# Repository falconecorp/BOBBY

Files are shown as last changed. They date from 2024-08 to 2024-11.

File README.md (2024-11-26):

# BOBBY
Bobby es un robot construido para competir en los juegos bonaerenses, en la categoría de Triatlón( Quita obstaculos - Sumo - Seguidor de linea ), por los estudiantes, Iago Botto, Dante Abel Canale, Lautaro Lammers y Lucas Chavez

[img_20240703_164955.md](https://github.com/user-attachments/files/17923314/img_20240703_164955.md)

## FUNCIONAMIENTO

### Seguidor de linea:
  Tenemos un sistema de sensores reflectivos QRE1113GR, en configuracion de array, que permite detectar con precisión, una linea blanca que representa el camino, y debemos recorrerlo en el menor tiempo posible
Utilizamos un algorimo de PD
~~~
  uint8_t PID(){
    int error = setpoint - lecturaQRE();
    int P = error * Kp;
    int D = (error - ultimo_error) * Kd;
    ultimo_error = error;
    float output = P + D;
    output = abs(output);
    output = map(output, 0, 25000, 0, limite_output);
    output = constrain(output, 0, limite_output);
    return (output);
  }
~~~
que nos permite poder variar los valores PWM enviados al motor, para seguir la linea correctamente

### Quita Obstáculos
  Nos encontramos con 5 sensores GP2Y0A02YK0F de distancia, que con un algoritmo y filtro digital, verificamos si hay un objeto o no. Agregado a esto, se utilizan 3 sensores de piso QRE1113GR, para evitar caernos de la pista
cuando atacamos a cada obstáculo.

### Sumo
  Aqui tenemos a nuestra categoría estrella, en esta disciplina, el robot es controlado por el usuario a través de una conexión Bluetooth entre un joystick de Ps3, y un modulo ESP32. Se compite contra otro robot en las mismas condiciones en un tatami.

## INFORME DE COSTES
#### Sensores
  -Sharp GP2Y0A02YK0F: 10.509$ c/u (starware)  (x5)    
  -Sensores de piso QRE1113GR: 969.37$ c/u (mouser)  (x8)    
  -impresion 3D: 8.000$ (300 gr)    
  -Motores AP&S SP6-260: 26.000$ c/u (AP&S)  (x2)    
  -Controladores BTS7960: 20.0000$ c/u (MercadoLibre)  (x2)    
  -ESP32: 7.329$ c/u (Starware)   (x1)    
  -Conexionado y cables: 20.000$ (it&t)    
#### Costo total: 187.626$
## FALLAS Y COSAS A MEJORAR
### organización
  -Problemas en el cálculo de tiempos.    
  -incumplimientos de los plazos acordados.    
  -falta de compromiso con el proyecto.    
  -falta de conocimientos previos para un proyecto de este calibre.    
  -subestimacion de los demas competidores.    

### programación
  Sumo: no hubo problemas mayores.    
  Seguidor de linea:    
    - dificultades a la hora de modificar valores de PID y varios.    
    - eleccion de sensores que complicaron las pruebas(QRE1113GR) necesita una distancia con respecto al piso muy pequeña.    
  Quita Obstáculos:    
    - no dedicarle tiempo a esta disciplina, lo que nos puso en desventaja con respecto a los otros.    
    - problemas en la estructura de manejo de sensores.    
    - problemas en la detección del limite de pista, debido a la altura incorrecta de los QRE1113GR

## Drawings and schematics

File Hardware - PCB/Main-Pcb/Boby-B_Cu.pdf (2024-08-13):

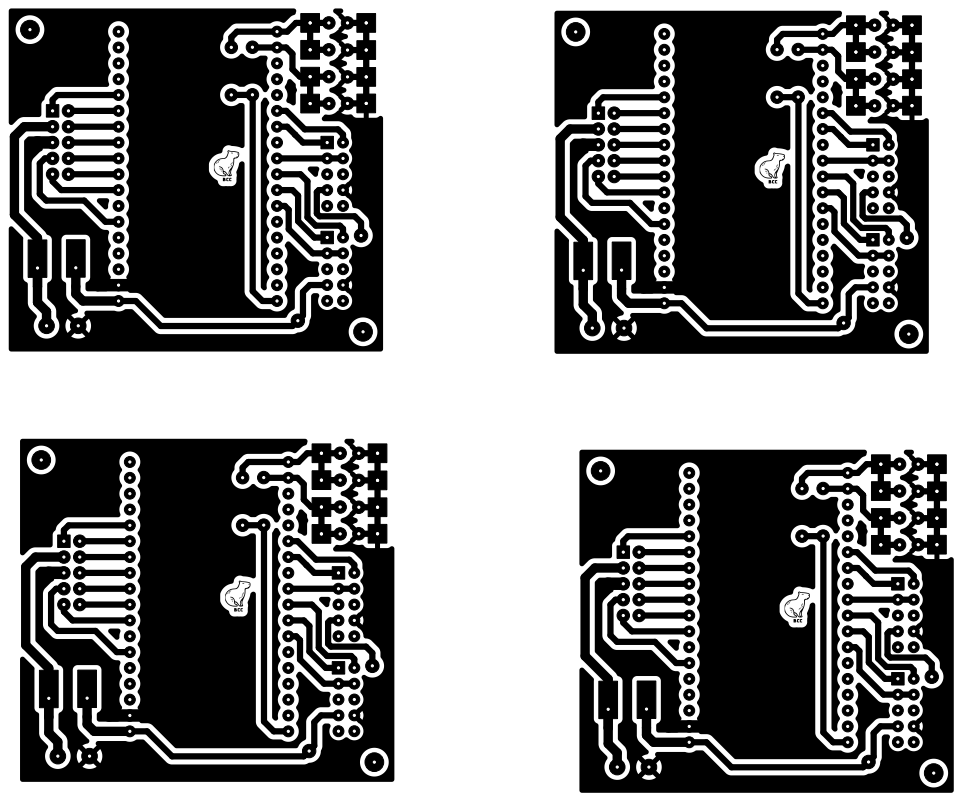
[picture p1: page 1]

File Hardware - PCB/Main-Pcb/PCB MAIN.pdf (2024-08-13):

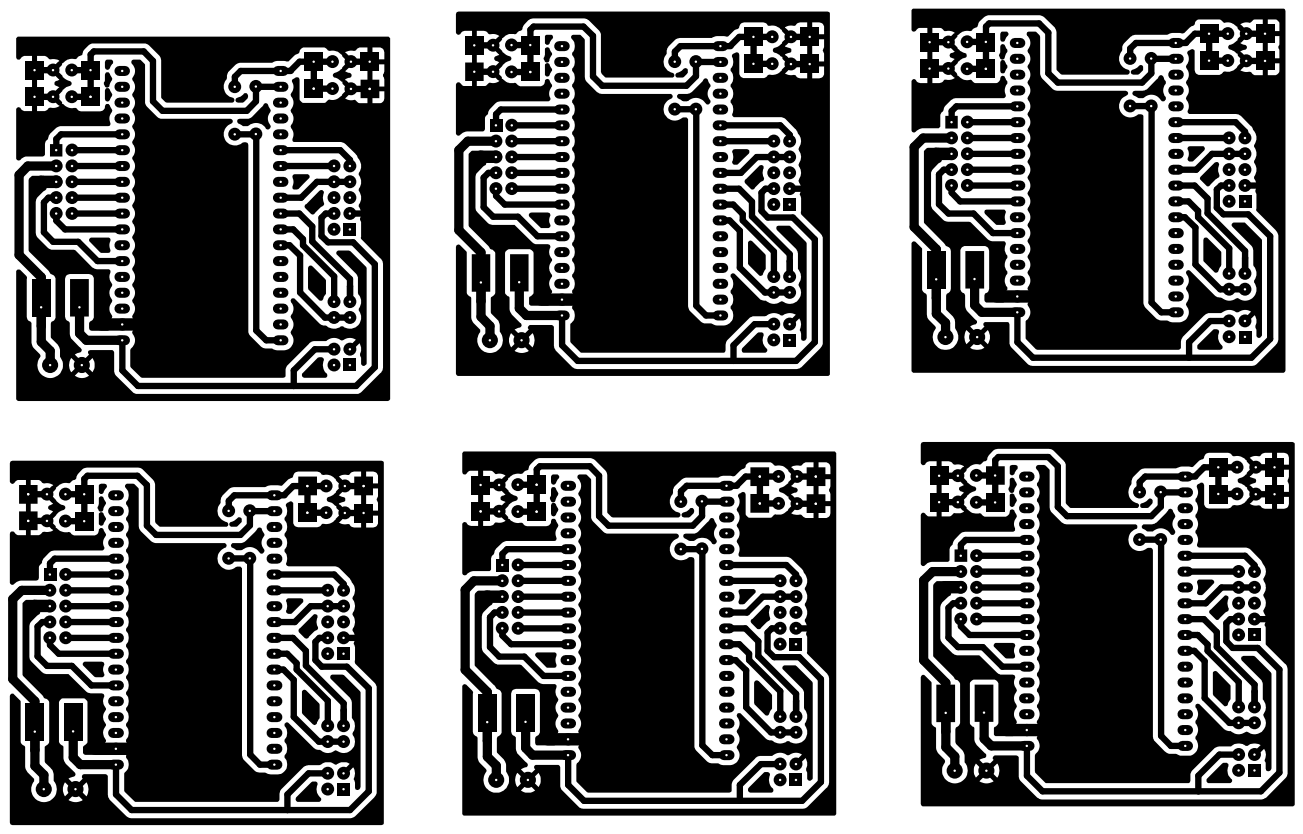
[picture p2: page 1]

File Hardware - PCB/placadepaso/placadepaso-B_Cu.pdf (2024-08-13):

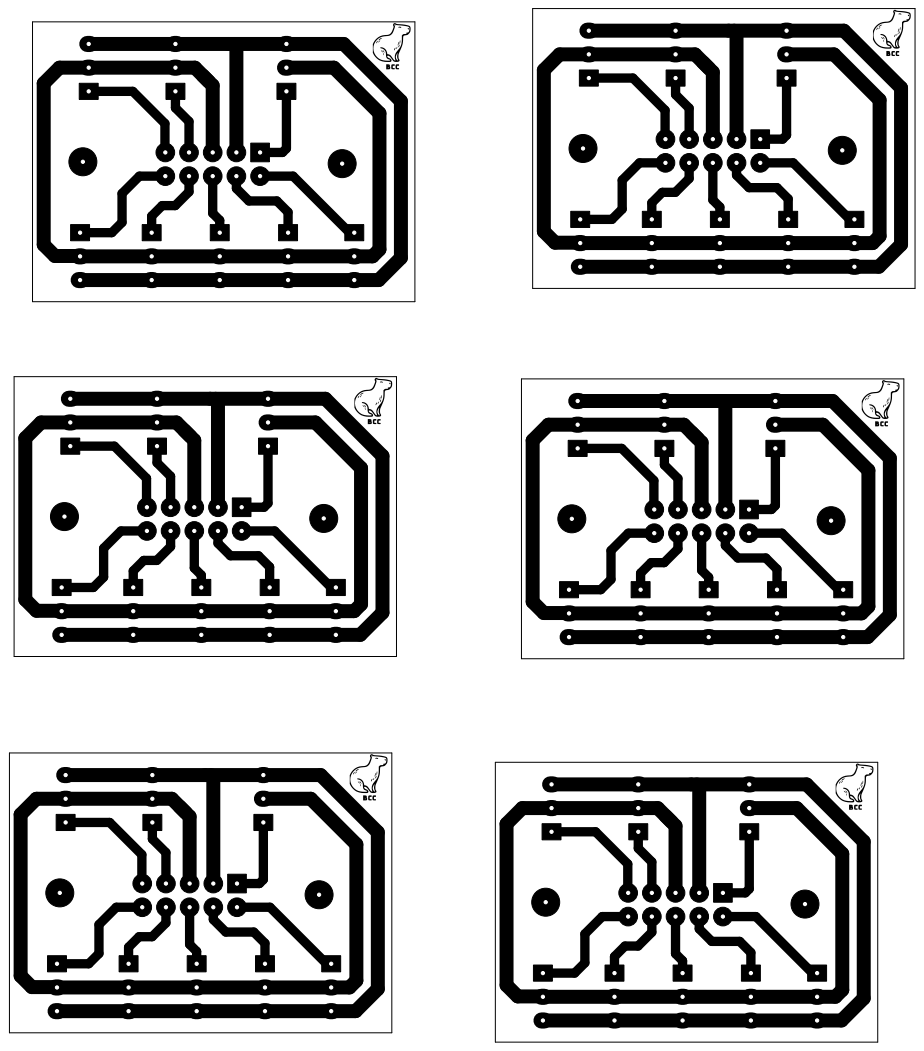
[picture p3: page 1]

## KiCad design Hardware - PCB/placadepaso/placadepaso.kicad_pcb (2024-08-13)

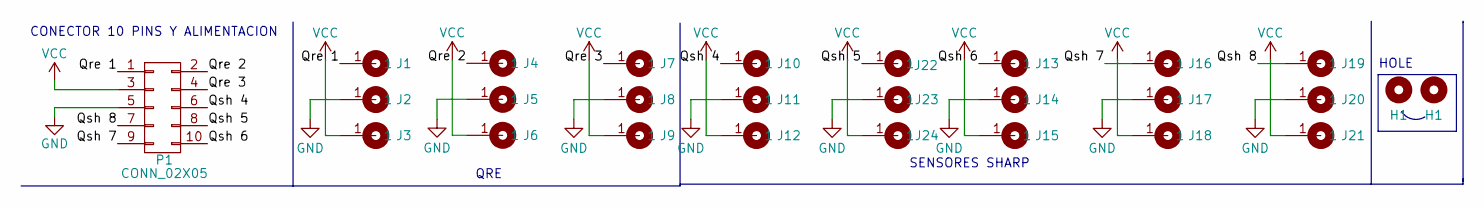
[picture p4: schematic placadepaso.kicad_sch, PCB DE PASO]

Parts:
H1: Mounting_Hole; Tornillo_M3_8mm
J1, J2, J3, J4, J5, J6, J7, J8, J9, J10, J11, J12, J13, J14, J15, J16, J17, J18, J19, J20, J21, J22, J23, J24: Cable_PAD; Cable_Doble_1,5mm_little
P1: CONN_02X05; Header_2x05x2.54mm_Vertical

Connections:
/Qre 1: J1.1, P1.1
/Qre 2: J4.1, P1.2
/Qre 3: J7.1, P1.4
/Qsh 4: J10.1, P1.6
/Qsh 5: J22.1, P1.8
/Qsh 6: J13.1, P1.10
/Qsh 7: J16.1, P1.9
/Qsh 8: J19.1, P1.7
GND: J2.1, J5.1, J8.1, J11.1, J14.1, J17.1, J20.1, J23.1, P1.5
VCC: J3.1, J6.1, J9.1, J12.1, J15.1, J18.1, J21.1, J24.1, P1.3

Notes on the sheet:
HOLE
QRE
CONECTOR 10 PINS Y ALIMENTACION
SENSORES SHARP

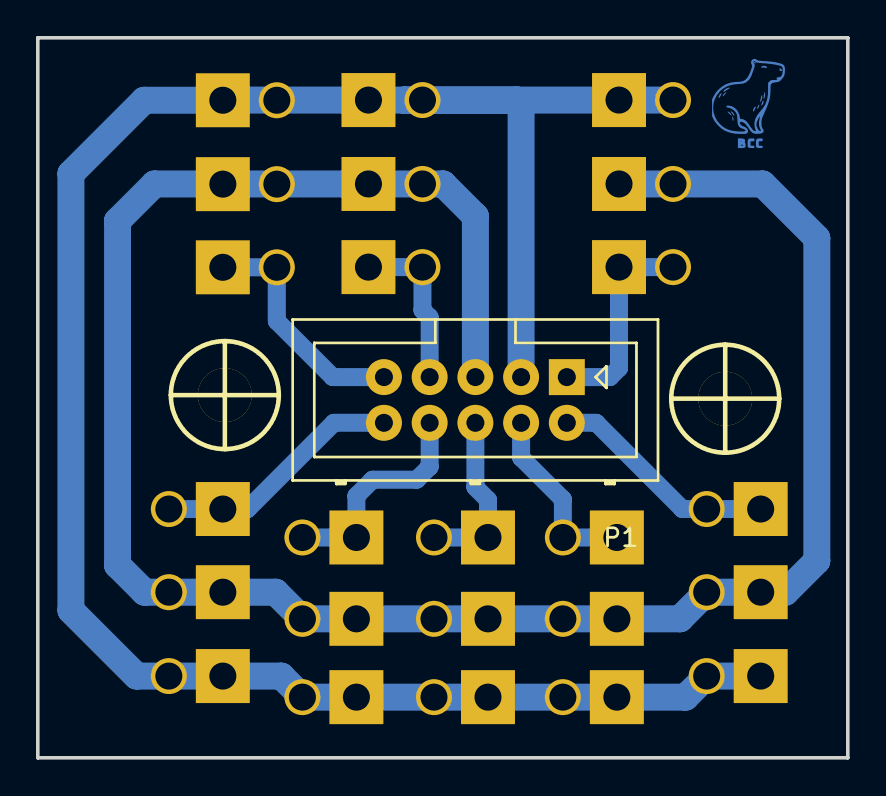
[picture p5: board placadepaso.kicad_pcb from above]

Board: 2 copper layers, 45.0 x 40.0 mm, 27 parts (0 on the bottom side), 10 nets.

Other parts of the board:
H2: Mounting_Hole; Tornillo_M3_8mm

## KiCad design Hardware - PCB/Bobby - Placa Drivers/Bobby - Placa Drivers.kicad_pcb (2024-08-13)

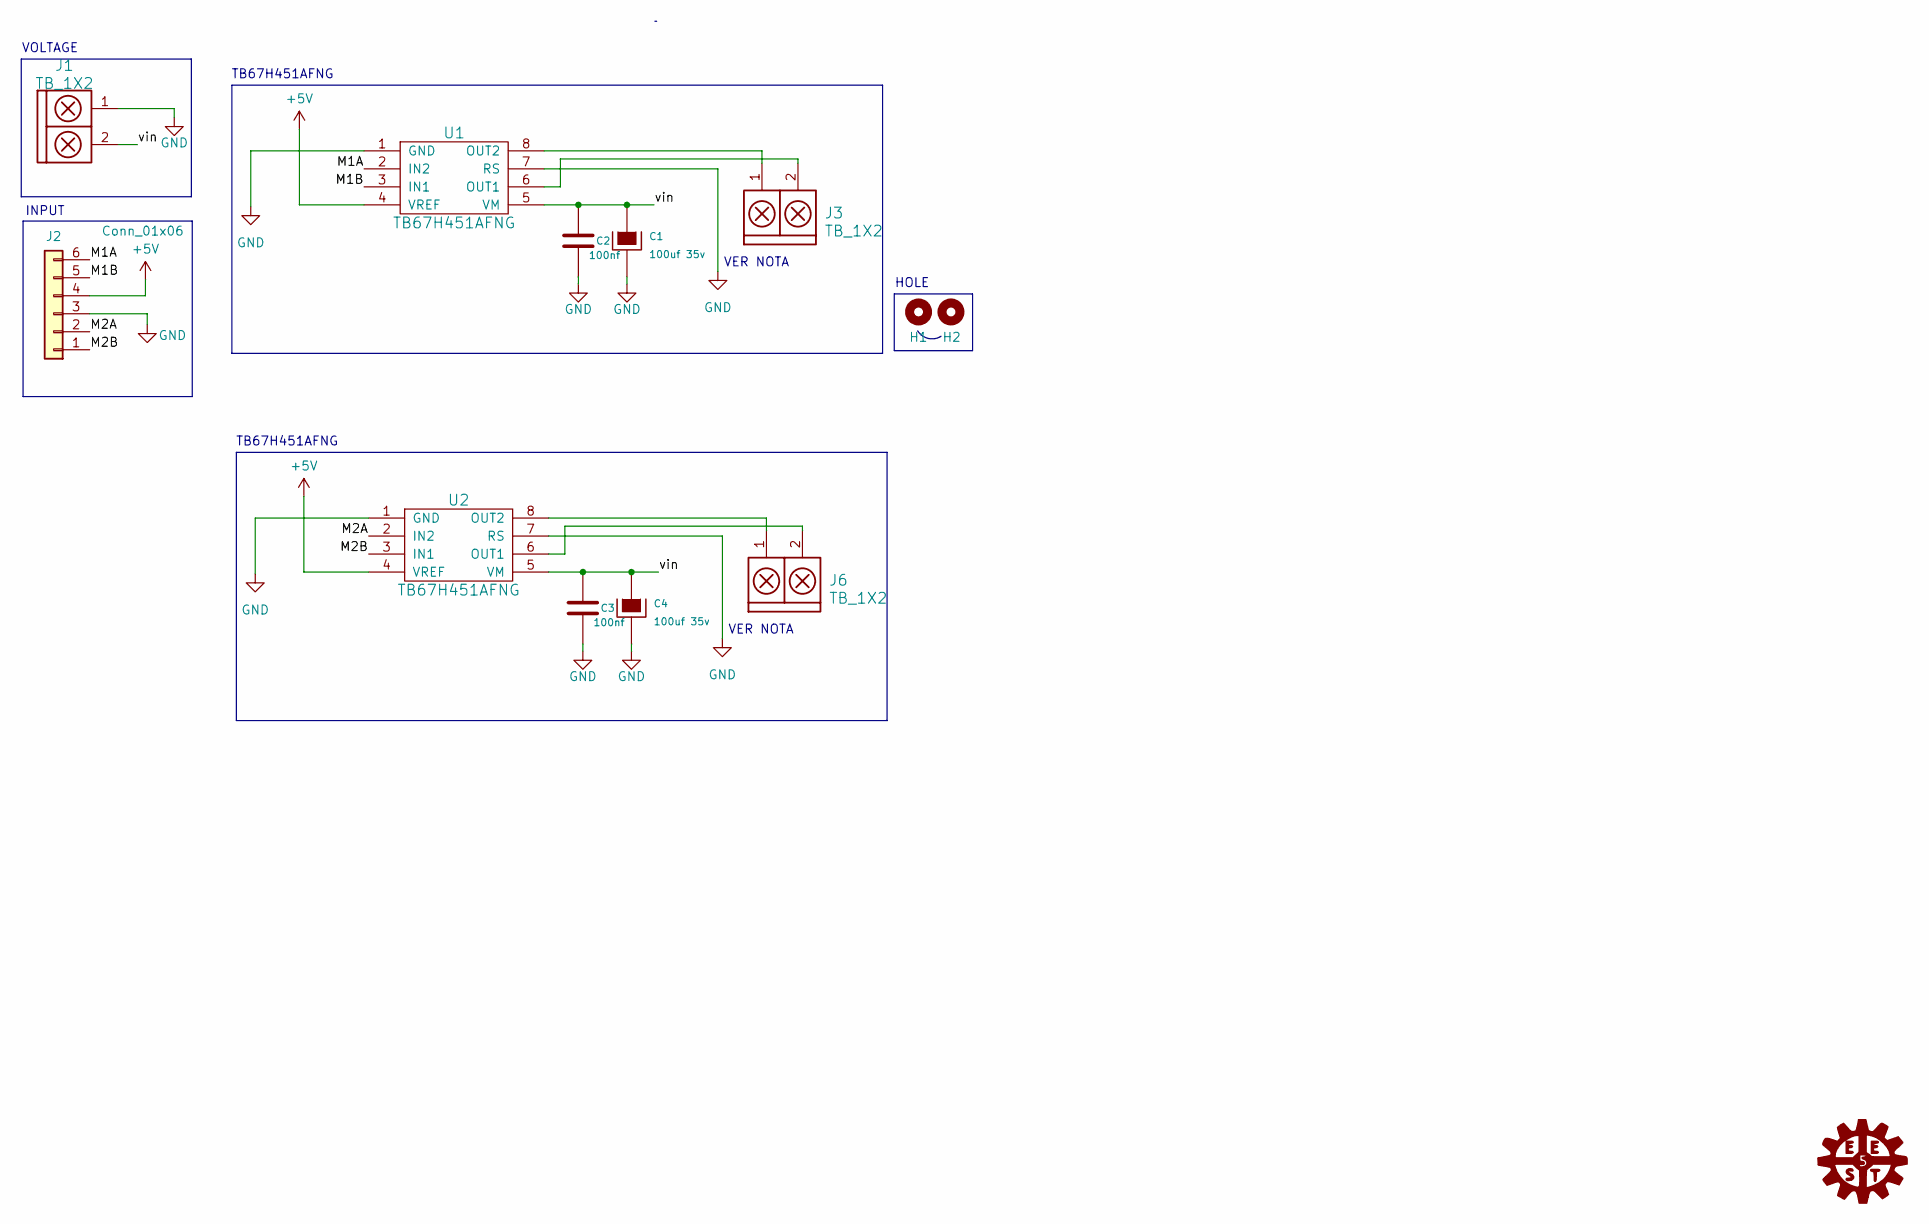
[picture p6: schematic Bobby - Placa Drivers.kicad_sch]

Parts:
C1, C4: 100uf 35v; CAP_ELEC_10X8mm
C2, C3: 100nf; C_1206
H1, H2: Mounting_Hole; Tornillo_M3_8mm
J1, J3, J6: TB_1X2; BORNERA2_AZUL
J2: Conn_01x06; FanPinHeads_1x6_P2.54mm_Vertical
U1, U2: TB67H451AFNG; SSOP-8

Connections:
+5V: U1.4 (VREF), U2.4 (VREF); also elsewhere on the board
/M1A: U1.2 (IN2); also elsewhere on the board
/M1B: U1.3 (IN1); also elsewhere on the board
/M2A: U2.2 (IN2); also elsewhere on the board
/M2B: U2.3 (IN1); also elsewhere on the board
/vin: C1.1, C2.1, C3.1, C4.1, J1.2, U1.5 (VM), U2.5 (VM)
GND: C1.2, C2.2, C3.2, C4.2, J1.1, U1.1 (GND), U1.7 (RS), U2.1 (GND), U2.7 (RS); also elsewhere on the board
unnamed: J3.2, U1.6 (OUT1)
unnamed: J3.1, U1.8 (OUT2)
unnamed: J6.2, U2.6 (OUT1)
unnamed: J6.1, U2.8 (OUT2)

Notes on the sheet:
HOLE
VER NOTA
INPUT
TB67H451AFNG
VOLTAGE

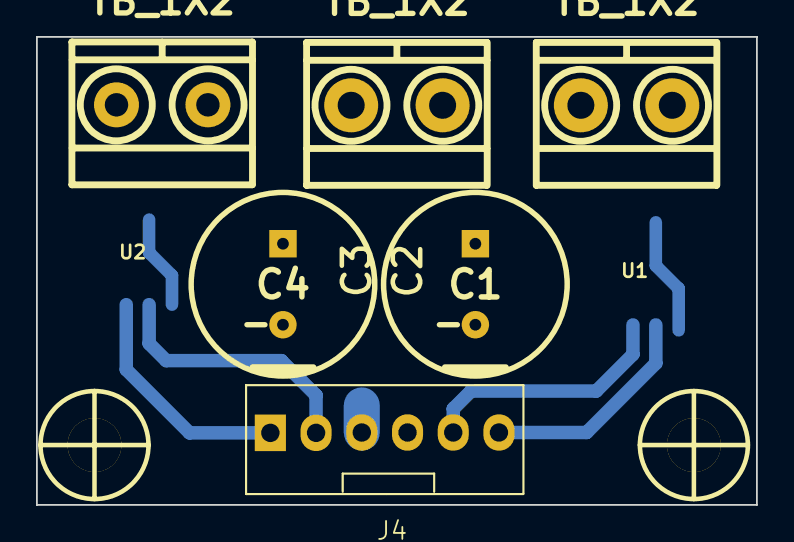
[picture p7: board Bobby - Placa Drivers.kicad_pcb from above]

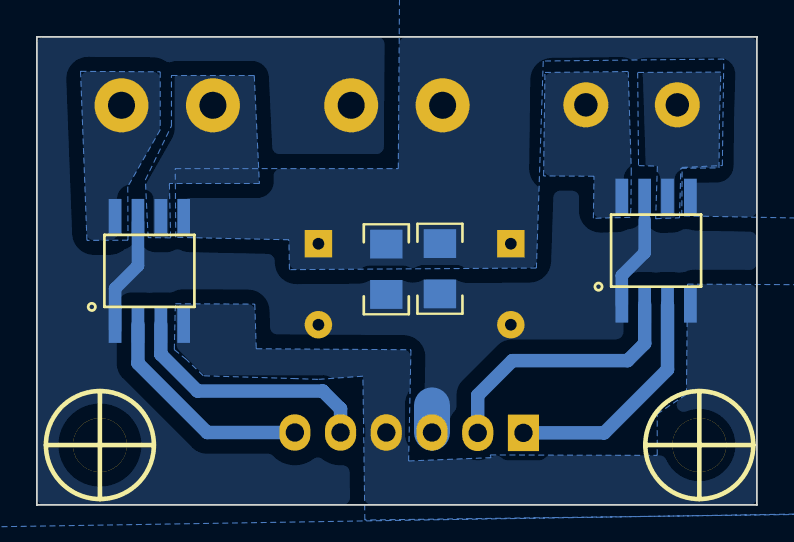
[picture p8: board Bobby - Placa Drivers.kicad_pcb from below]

Board: 2 copper layers, 40.0 x 26.0 mm, 12 parts (5 on the bottom side), 11 nets.

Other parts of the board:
J4: Conn_01x06; FanPinHeads_1x6_P2.54mm_Vertical

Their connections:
+5V: J4.4; also elsewhere on the board
/M1A: J4.6; also elsewhere on the board
/M1B: J4.5; also elsewhere on the board
/M2A: J4.2; also elsewhere on the board
/M2B: J4.1; also elsewhere on the board
GND: J4.3; also elsewhere on the board

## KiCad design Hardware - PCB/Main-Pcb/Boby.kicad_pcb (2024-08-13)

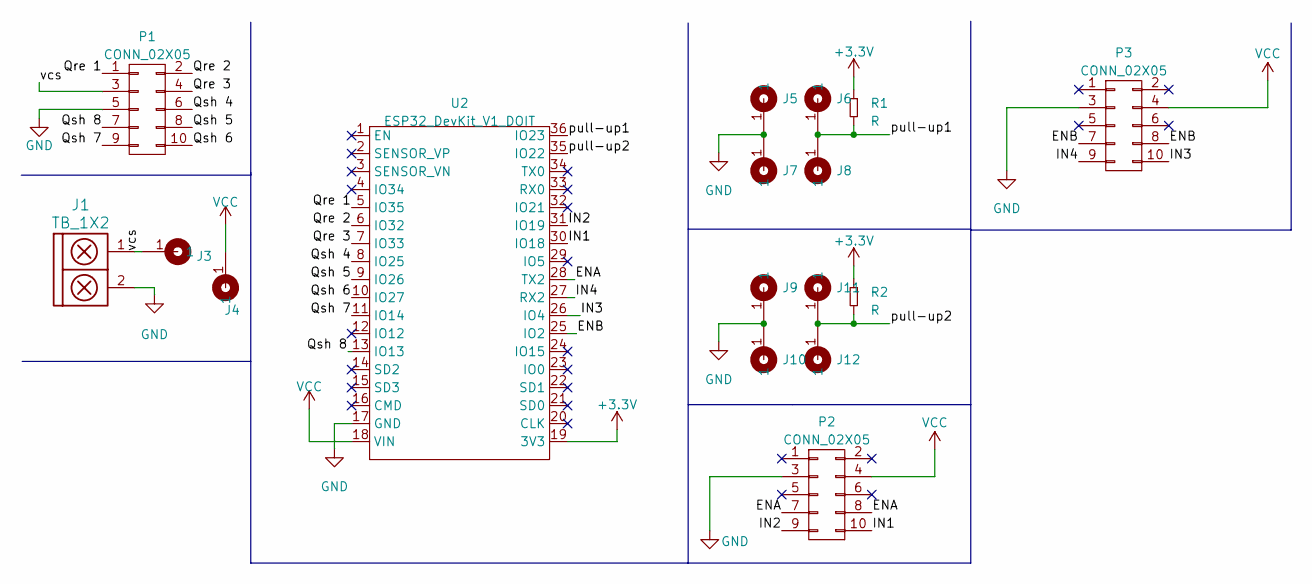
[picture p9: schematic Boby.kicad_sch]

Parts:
J1: TB_1X2; BORNERA2_AZUL
J3, J4: Cable_PAD; Cable_1,5mm
J5, J6, J7, J8, J9, J10, J11, J12: Cable_PAD; Cable_Doble_1,5mm_little
P1, P2, P3: CONN_02X05; Header_2x05x2.54mm_Vertical
R1, R2: R; RES0.3
U2: ESP32_DevKit_V1_DOIT; ESP32_DEVKIT_V1_DOIT

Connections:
+3.3V: R1.1, R2.1, U2.19 (3V3)
/ENA: P2.7, P2.8, U2.28 (TX2)
/ENB: P3.7, P3.8, U2.25 (IO2)
/IN1: P2.10, U2.30 (IO18)
/IN2: P2.9, U2.31 (IO19)
/IN3: P3.10, U2.26 (IO4)
/IN4: P3.9, U2.27 (RX2)
/Qre 1: P1.1, U2.5 (IO35)
/Qre 2: P1.2, U2.6 (IO32)
/Qre 3: P1.4, U2.7 (IO33)
/Qsh 4: P1.6, U2.8 (IO25)
/Qsh 5: P1.8, U2.9 (IO26)
/Qsh 6: P1.10, U2.10 (IO27)
/Qsh 7: P1.9, U2.11 (IO14)
/Qsh 8: P1.7, U2.13 (IO13)
/pull-up1: J6.1, J8.1, R1.2, U2.36 (IO23)
/pull-up2: J11.1, J12.1, R2.2, U2.35 (IO22)
/vcs: J1.1, J3.1, P1.3
GND: J1.2, J5.1, J7.1, J9.1, J10.1, P1.5, P2.3, P3.3, U2.17 (GND)
VCC: J4.1, P2.4, P3.4, U2.18 (VIN)

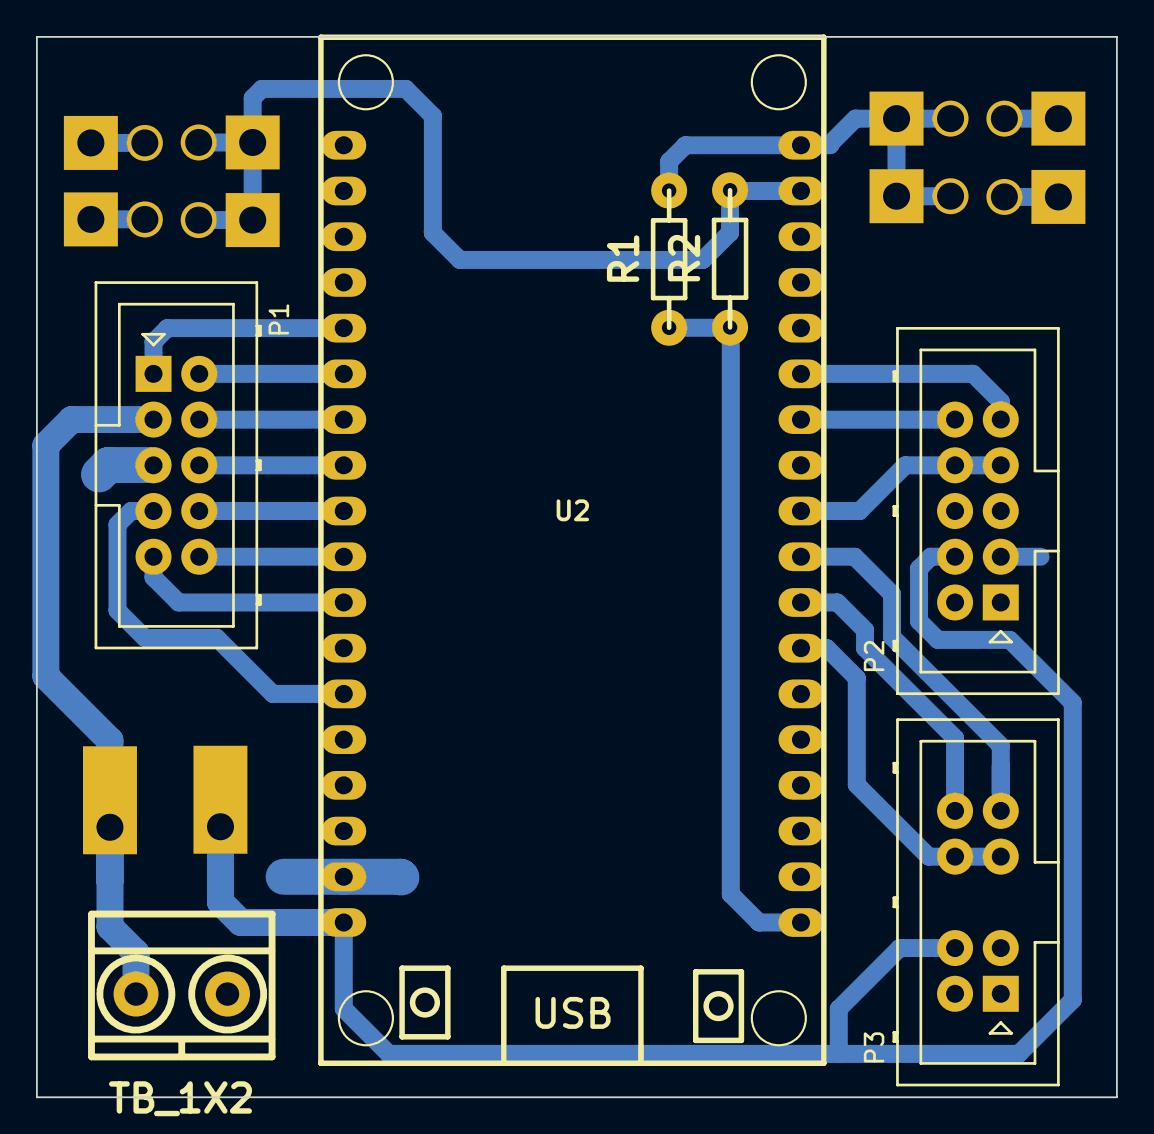
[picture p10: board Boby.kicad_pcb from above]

Board: 2 copper layers, 60.0 x 58.9 mm, 17 parts (0 on the bottom side), 20 nets.

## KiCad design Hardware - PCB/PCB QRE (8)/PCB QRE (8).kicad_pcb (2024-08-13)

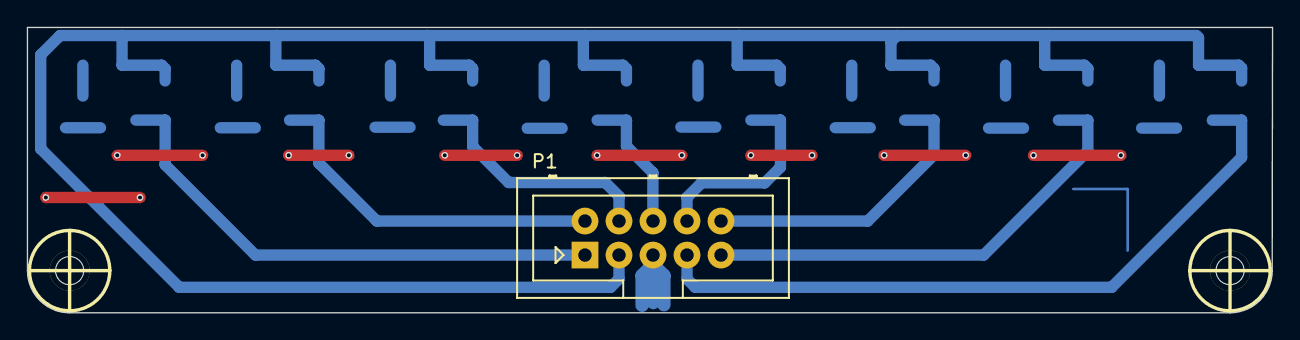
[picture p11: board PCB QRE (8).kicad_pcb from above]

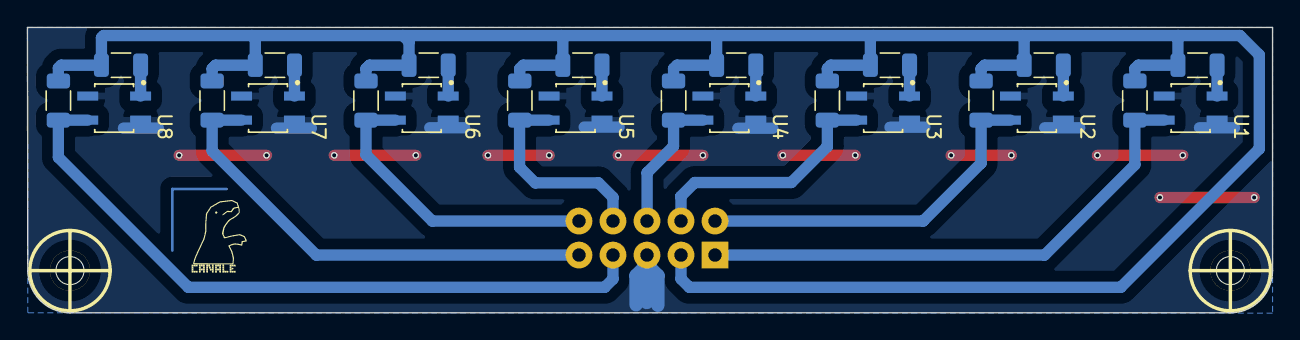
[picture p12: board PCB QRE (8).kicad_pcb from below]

Board: 2 copper layers, 93.0 x 21.3 mm, 29 parts (24 on the bottom side), 18 nets.

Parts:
H1, H2: Mounting_Hole; MountingHole_2.1mm
P1: CONN_02X05; Header_2x05x2.54mm_Vertical
R1, R3, R5, R7, R9, R11, R13, R15: 100; R_1206_3216Metric
R2, R4, R6, R8, R10, R12, R14, R16: 240; R_1206_3216Metric
U1, U2, U3, U4, U5, U6, U7, U8: QRE1113GR; SOIC180P460X187-4N
hole_3mm, hole_3mm#2: VAL**; hole_3mm

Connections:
/PIN1: P1.1, R2.1, U1.3
/PIN2: P1.2, R4.1, U2.3
/PIN3: P1.4, R6.1, U3.3
/PIN4: P1.6, R8.1, U4.3
/PIN5: P1.8, R10.1, U5.3
/PIN6: P1.10, R12.1, U6.3
/PIN7: P1.9, R14.1, U7.3
/PIN8: P1.7, R16.1, U8.3
GND: P1.5, U1.2, U1.4, U2.2, U2.4, U3.2, U3.4, U4.2, U4.4, U5.2, U5.4, U6.2, U6.4, U7.2, U7.4, U8.2, U8.4
unnamed: R1.1, U1.1
unnamed: R3.1, U2.1
unnamed: R5.1, U3.1
unnamed: R7.1, U4.1
unnamed: R9.1, U5.1
unnamed: R11.1, U6.1
unnamed: R13.1, U7.1
unnamed: R15.1, U8.1
VCC: P1.3, R1.2, R2.2, R3.2, R4.2, R5.2, R6.2, R7.2, R8.2, R9.2, R10.2, R11.2, R12.2, R13.2, R14.2, R15.2, R16.2

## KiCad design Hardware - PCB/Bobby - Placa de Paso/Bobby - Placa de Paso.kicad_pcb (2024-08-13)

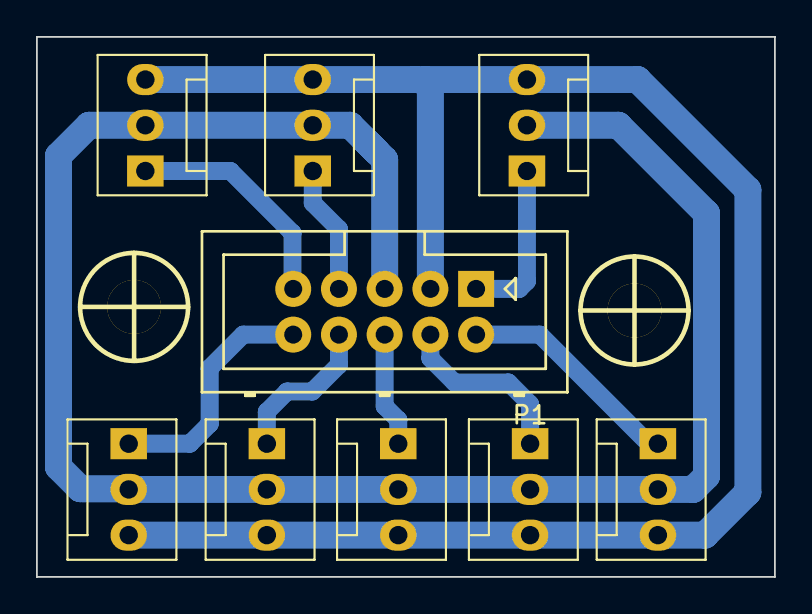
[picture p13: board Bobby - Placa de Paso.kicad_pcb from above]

Board: 2 copper layers, 41.0 x 30.0 mm, 11 parts (0 on the bottom side), 10 nets.

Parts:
H1, H2: Mounting_Hole; Tornillo_M3_8mm
P1: CONN_02X05; Header_2x05x2.54mm_Vertical
QRE1, QRE2, QRE3: CONN_01X03; FanPinHeader_1x03_P2.54mm_Vertical
QSH4, QSH5, QSH6, QSH7, QSH8: CONN_01X03; FanPinHeader_1x03_P2.54mm_Vertical

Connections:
/Qre 1: P1.1, QRE1.1
/Qre 2: P1.2, QRE2.1
/Qre 3: P1.4, QRE3.1
/Qsh 4: P1.6, QSH4.1
/Qsh 5: P1.8, QSH5.1
/Qsh 6: P1.10, QSH6.1
/Qsh 7: P1.9, QSH7.1
/Qsh 8: P1.7, QSH8.1
GND: P1.5, QRE1.2, QRE2.2, QRE3.2, QSH4.2, QSH5.2, QSH6.2, QSH7.2, QSH8.2
VCC: P1.3, QRE1.3, QRE2.3, QRE3.3, QSH4.3, QSH5.3, QSH6.3, QSH7.3, QSH8.3

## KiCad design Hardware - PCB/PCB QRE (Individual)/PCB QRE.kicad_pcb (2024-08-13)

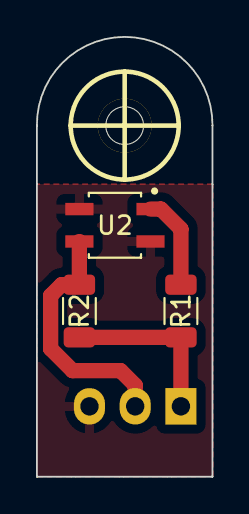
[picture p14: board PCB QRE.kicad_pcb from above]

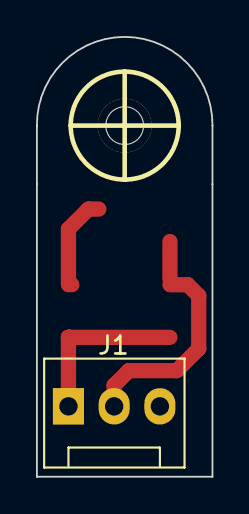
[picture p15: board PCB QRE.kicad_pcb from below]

Board: 2 copper layers, 9.8 x 24.4 mm, 5 parts (2 on the bottom side), 4 nets.

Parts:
J1: Conn_01X03; FanPinHeader_1x03_P2.54mm_Vertical
R1: 100; R_1206_3216Metric
R2: 240; R_1206_3216Metric
U2: QRE1113GR; SOIC180P460X187-4N
hole_3mm: VAL**; hole_3mm

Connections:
GND: J1.3, U2.2, U2.4
unnamed: J1.2, R2.1, U2.3
unnamed: R1.1, U2.1
VCC: J1.1, R1.2, R2.2

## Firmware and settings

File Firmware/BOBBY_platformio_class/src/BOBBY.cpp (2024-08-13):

#include <stdint.h>
#include <iostream>
#include <Ps3Controller.h>
#include <BluetoothSerial.h>
#define VALUE_0_01 0.01
#define VALUE_0_1 0.1
#define N 100
#define FREC 800
#define RES 8
#define CHANNEL1 1
#define CHANNEL2 2
#define CHANNEL3 3
#define CHANNEL4 4
#define PIN_MOTOR_A1 5
#define PIN_MOTOR_B1 16
#define PIN_MOTOR_B2 17
#define PIN_MOTOR_A2 18
#define PIN_BOTON 22
int tolerancia = 35;
float COMPENSACION_POS = 1.2;
float COMPENSACION_NEG = 1.3;
bool DEBUG = 0;
bool boton_presionado = false;
BluetoothSerial BT;
void setup() {
  Serial.begin(256000);
  Ps3.begin("00:00:00:00:00:00");
  delay(2000);
  ledcSetup(CHANNEL1, FREC, RES);
  ledcSetup(CHANNEL2, FREC, RES);
  ledcSetup(CHANNEL3, FREC, RES);
  ledcSetup(CHANNEL4, FREC, RES);
  ledcAttachPin(PIN_MOTOR_A1, CHANNEL1);
  ledcAttachPin(PIN_MOTOR_A2, CHANNEL2);
  ledcAttachPin(PIN_MOTOR_B1, CHANNEL3); 
  ledcAttachPin(PIN_MOTOR_B2, CHANNEL4);
  pinMode(32, INPUT);
  pinMode(33, INPUT);
  pinMode(25, INPUT);
  pinMode(26, INPUT);
  pinMode(27, INPUT);
  pinMode(14, INPUT);
  pinMode(12, INPUT);
  pinMode(13, INPUT);
}

///////////////////////////////////////////////////////////////////////////////////////////
///////////////////////////////////////////////////////////////////////////////////////////

/////////////////////////////  LINE FOLLOWER   ////////////////////////////////////////////

///////////////////////////////////////////////////////////////////////////////////////////
///////////////////////////////////////////////////////////////////////////////////////////

enum class direccion_enumerada{
  FRENAR,
  ADELANTE,
  DERECHA,
  IZQUIERDA
};
struct retorno_linea{
  direccion_enumerada direccion;
  uint8_t velocidad;
};  
class Line_follower{
private:
  uint8_t vel_base = 90;
  uint8_t vel_pos;
  uint8_t vel_neg;
  uint8_t vel_max = 90;
  uint16_t setpoint = 21000;
  uint8_t Kp=1.3, Kd=0.6;
  uint8_t limite_output = 70;
  uint16_t error;
  uint16_t ultimo_error;
  uint8_t tolerancia = 35;
  retorno_linea estado_motor;
public:
  uint16_t lectura_qre();
  uint8_t PID();
  void control_linea();
  void movimiento_linea();
  void valor_motor();
  void menuBT();
  //Line_follower(uint8_t _kp, uint8_t _kd);
};
/*
Line_follower::Line_follower(uint8_t _kp, uint8_t _kd):Kp(_kp),Kd(_kd)
{
  
}
*/
uint16_t Line_follower::lectura_qre() {
  uint16_t qre1, qre2, qre3, qre4, qre5, qre6, qre7, qre8;
  qre1 = analogRead(32);
  qre2 = analogRead(33);
  qre3 = analogRead(25);
  qre4 = analogRead(26);
  qre5 = analogRead(27);
  qre6 = analogRead(14);
  qre7 = analogRead(12);
  qre8 = analogRead(13);
  uint16_t valor_qre = (qre1 + qre2 + qre3 + qre4 + qre5 + qre6 + qre7 + qre8);
  if(DEBUG){
  BT.print("qre:");
  BT.println(valor_qre);
  }
  return valor_qre;
}
uint8_t Line_follower::PID(){
  error = setpoint - lectura_qre();
  int P = error * Kp;
  int D = (error - ultimo_error) * Kd;
  ultimo_error = error;
  if(DEBUG){
    BT.print("error: ");
    BT.println(error);
  }
  float output = P + D;
  output = abs(output);
  output = map(output, 0, 28000, 0, limite_output);
  output = constrain(output, 0, limite_output);
  return output;
}
void Line_follower::valor_motor(){
  uint8_t vel_motor = estado_motor.velocidad;
  vel_pos = vel_base + vel_motor;
  vel_neg = vel_base - vel_motor;
  vel_pos = vel_pos * COMPENSACION_POS;
  vel_neg = vel_neg / COMPENSACION_NEG;
    if(vel_neg < tolerancia){
    vel_neg = 0;
  }
  vel_pos = constrain(vel_pos, 0, 255);
  vel_neg = constrain(vel_neg, 0, 255);
}
void Line_follower::control_linea() {
  PID();
  int lim = 2800;
  int lim_neg = -2800;
  if (error < lim_neg) {
    estado_motor.direccion = direccion_enumerada::DERECHA;
    estado_motor.velocidad = PID();
  } else if (error > lim) {
    estado_motor.direccion = direccion_enumerada::IZQUIERDA;
    estado_motor.velocidad = PID();
  } else {
    estado_motor.direccion = direccion_enumerada::ADELANTE;
    estado_motor.velocidad = PID();
  }
}
void Line_follower::movimiento_linea() {
  control_linea();
  switch (estado_motor.direccion)
  {
    case direccion_enumerada::DERECHA:
    {  
      valor_motor();
      ledcWrite(CHANNEL1, LOW);
      ledcWrite(CHANNEL2, vel_pos);
      ledcWrite(CHANNEL3, LOW);
      ledcWrite(CHANNEL4, vel_neg);
      if(DEBUG){
      BT.println("derecha");
      BT.print("vel_pos: ");      
      BT.println(vel_pos);
      BT.print("vel_neg: ");  
      BT.println(vel_neg);
      }  
      break;
    }
    case direccion_enumerada::IZQUIERDA:
    {
      valor_motor();
      ledcWrite(CHANNEL1, LOW);
      ledcWrite(CHANNEL2, vel_neg);
      ledcWrite(CHANNEL3, LOW);
      ledcWrite(CHANNEL4, vel_pos);      
      if(DEBUG){
      BT.println("izquierda");
      BT.print("vel_pos: ");      
      BT.println(vel_pos);
      BT.print("vel_neg: ");  
      BT.println(vel_neg);
      }
    }
    case direccion_enumerada::ADELANTE:
    {
      ledcWrite(CHANNEL1, LOW);
      ledcWrite(CHANNEL2, vel_max);
      ledcWrite(CHANNEL3, LOW);
      ledcWrite(CHANNEL4, vel_max);  
      if(DEBUG){
        BT.println("Adelante");
      }
      break;
    }
  }
}

void Line_follower::menuBT(){
  if (BT.available())
  { 
    char Message = BT.read();
    switch (Message)
    {
      case 'Q':
      {
        Kp += VALUE_0_1;
        BT.print("Kp: ");
        BT.println(Kp);
        break;
      }
      case 'W':
      {
        Kp -= VALUE_0_1;
        BT.print("Kp: ");
        BT.println(Kp);
        break;
      }
      case 'E':
      {
        Kp += VALUE_0_01;
        BT.print("Kp: ");
        BT.println(Kp);
        break;
      }
      case 'R':
      {
        Kp -= VALUE_0_01;
        BT.print("Kp: ");
        BT.println(Kp);
        break;
      }
      case 'T':
      {
        Kd += VALUE_0_1;
        BT.print("Kd: ");
        BT.println(Kd);
        break;
      }
      case 'Y':
      {
        Kd -= VALUE_0_1;
        BT.print("Kd: ");
        BT.println(Kd);
        break;
      }
      case 'U':
      {
        Kd += VALUE_0_01;
        BT.print("Kd: ");
        BT.println(Kd);
        break;
      }
      case 'I':
      {
        Kd -= VALUE_0_01;
        BT.print("Kd: ");
        BT.println(Kd);
        break;
      }
      case 'O':
      {
        vel_base += 10;
        BT.print("Velocidad base: ");
        BT.println(vel_base);
        break;
      }
      case 'P':
      {
        vel_base -= 10;
        BT.print("Velocidad base: ");
        BT.println(vel_base);
        break;
      }
      case 'A':
      {
        setpoint += 1000;
        BT.print("setpoint: ");
        BT.println(setpoint);
        break;
      }
      case 'S':
      {
        setpoint -= 1000;
        BT.print("setpoint: ");
        BT.println(setpoint);
        break;
      }
      case 'D':
      {
        tolerancia += 5;
        BT.print("Tolerancia: ");
        BT.println(tolerancia);
        break;
      }
      case 'F':
      {
      tolerancia -=5;
        BT.print("Tolerancia: ");
        BT.println(tolerancia);
        break;
      }
      case 'G':
      {
        limite_output += 5;
        BT.print("limite output: ");
        BT.println(limite_output);
        break;
      }
      case 'H':
      {
      limite_output -= 5;
        BT.print("limite output: ");
        BT.println(limite_output);
        break;
      }            
      case 'J':
      {
        DEBUG = 1;
        BT.print("DEBUG: ");
        BT.println(DEBUG);
        break;
      }
      case 'K':
      {
        DEBUG = 0;
        BT.print("DEBUG: ");
        BT.println(DEBUG);
        break;
      }
    }
  }
}
///////////////////////////////////////////////////////////////////////////////////////////
///////////////////////////////////////////////////////////////////////////////////////////

////////////////////////////////   SUMO   /////////////////////////////////////////////////

///////////////////////////////////////////////////////////////////////////////////////////
///////////////////////////////////////////////////////////////////////////////////////////
enum class retorno_direccion{
  ADELANTE,
  ATRAS,
  DERECHA,
  IZQUIERDA,
  FRENAR
};
enum class retorno_motor{
  A,
  B
};
struct retorno_sumo{
  retorno_direccion direccion;
  retorno_motor motor; 
};
class sumo{
private:
  int8_t lim = 10;
  int8_t lim_neg = -10;
  uint16_t eje_y;
  char16_t direccion;
  char16_t motor;
  retorno_sumo estado_motor;
public:
  uint8_t lectura_stickA();
  uint8_t lectura_stickB();
  void control_sumo();
  void movimiento_sumo();
  void conexion_bt();
  void inicio();
};
uint8_t sumo::lectura_stickA(){
  eje_y = Ps3.data.analog.stick.ly;
  eje_y = abs(eje_y);
  if(Ps3.data.button.r2)
  {
    eje_y = eje_y * 2;
    return(eje_y);
  }
  else if (Ps3.data.button.l2)
  {
    eje_y = eje_y / 2;
    return(eje_y);
  }
  return(eje_y);    
}
uint8_t sumo::lectura_stickB(){
  eje_y = Ps3.data.analog.stick.ry;
  eje_y = abs(eje_y);
  if(Ps3.data.button.r2)
  {
    eje_y = eje_y * 2;
    return(eje_y);
  }
  else if (Ps3.data.button.l2)
  {
    eje_y = eje_y / 2;
    return(eje_y);
  }
  return(eje_y);         
}
void sumo::control_sumo(){
  int lim_neg = -20;
  int lim = 20;
  int eje_ly_comparacion = Ps3.data.analog.stick.ly * -1;
  if(eje_ly_comparacion < lim_neg)
  {  
    BT.println("ATRAS");
    estado_motor.direccion = retorno_direccion::ATRAS;
    estado_motor.motor = retorno_motor::A;
  }
  else if(eje_ly_comparacion > lim)
  {
    BT.println("ADELANTE");
    estado_motor.direccion = retorno_direccion::ADELANTE;
    estado_motor.motor = retorno_motor::A;
  }
  else
  {
    BT.println("FRENAR");
    estado_motor.direccion = retorno_direccion::FRENAR;
    estado_motor.motor = retorno_motor::A;
  }
  int eje_ry_comparacion = Ps3.data.analog.stick.ry * -1;
  if(eje_ry_comparacion < lim_neg)
  {
    BT.println("ATRAS");
    estado_motor.direccion = retorno_direccion::ATRAS;
    estado_motor.motor = retorno_motor::B;
  }
  else if(eje_ry_comparacion > lim)
  {
    BT.println("ADELANTE");
    estado_motor.direccion = retorno_direccion::ADELANTE;
    estado_motor.motor = retorno_motor::B;
  }
  else
  {
    BT.println("FRENAR");
    estado_motor.direccion = retorno_direccion::FRENAR;
    estado_motor.motor = retorno_motor::B;
  }

}
void sumo::movimiento_sumo(){
  control_sumo();
  switch(estado_motor.motor){
    case retorno_motor::A:
    {
      switch(estado_motor.direccion) 
      {
        case retorno_direccion::ADELANTE:
        {
          ledcWrite(CHANNEL1, LOW);
          ledcWrite(CHANNEL2, lectura_stickA());
          break;    
        }
        case retorno_direccion::ATRAS:
        {
          ledcWrite(CHANNEL1, lectura_stickA());
          ledcWrite(CHANNEL2, LOW);
          break;
        }
        case retorno_direccion::FRENAR:
        {
          ledcWrite(CHANNEL1, LOW);
          ledcWrite(CHANNEL2, LOW);
          break;
        }
      }
      break;
    }
    case retorno_motor::B:
    {
      switch(estado_motor.direccion) 
      {
        case retorno_direccion::ADELANTE:
        {
          ledcWrite(CHANNEL1, LOW);
          ledcWrite(CHANNEL2, lectura_stickB());   
          break;      
        }
        case retorno_direccion::ATRAS:
        {
          ledcWrite(CHANNEL1, lectura_stickB());
          ledcWrite(CHANNEL2, LOW);
          break;
        }
        case retorno_direccion::FRENAR:
        {
          ledcWrite(CHANNEL1, LOW);
          ledcWrite(CHANNEL2, LOW);
          break;
        }
      }
      break;
    }
  }
}
void sumo::conexion_bt(){
  Ps3.begin("00:00:00:00:00:00");
  if(!Ps3.isConnected())
  {
    Ps3.begin("00:00:00:00:00:00");
    delay(200);
  }
}
void sumo::inicio(){
  conexion_bt();
  movimiento_sumo();
}

sumo Luchador;
Line_follower Linea; // Crear un objeto de la clase Line_follower
void loop(){
  while(!boton_presionado){
    if(digitalRead(PIN_BOTON) == LOW){
      boton_presionado = true;
      delay(200);
    }
  }
  while(digitalRead(PIN_BOTON) == LOW){
  }
  Luchador.inicio();
}

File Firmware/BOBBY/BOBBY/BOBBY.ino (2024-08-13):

#include <Ps3Controller.h>
#include <BluetoothSerial.h>

BluetoothSerial BT;
//MOTOR
#define N 100
#define FREC 1000
#define RES 8
#define CHANNEL1 1
#define CHANNEL2 2
#define CHANNEL3 3
#define CHANNEL4 4
#define PIN_MOTOR_A1 19
#define PIN_MOTOR_A2 18
#define PIN_MOTOR_B1 4
#define PIN_MOTOR_B2 16
#define ENABLE 2

//modoSeleccion
#define PIN_BOTON_ROTAR 22
#define PIN_BOTON_SELECCIONAR 23

//modoQuitaObstaculos
#define OBJETO_IZQUIERDA 25
#define OBJETO_IZQUIERDA_MEDIO 13
#define OBJETO_MEDIO 35
#define OBJETO_DERECHA_MEDIO 26
#define OBJETO_DERECHA 36
#define BLANCO 2000
#define DOBLAR 150
#define VEL_MAX 255
#define OBJETO_DETECTADO 85
#define SI 1
#define NO 0
enum tipos_de_modo{
  REPOSO,
  SEGURIDAD,
  BUSCAR,
  ATACAR,
  REUBICAR
};
tipos_de_modo modos_quita;

//seleccion
#define DELAY_200 200
#define TIEMPO_SEGURIDAD 5000
#define TIEMPO_IMPRESION 50
#define NUMERO_MODOS 3

long tiempo=millis(); //tiempo antes de iniciar la lectura
bool DEBUG = 0;

bool boton_presionado = false;
int modo_actual = 0;
bool boton_confirmar_presionado = false;
bool modo_de_seleccion = false;
bool modo_seleccionado = false;

void botonInicio(){
  while(!boton_presionado){
    if(digitalRead(PIN_BOTON_ROTAR) == LOW){
    boton_presionado = true;
    delay(DELAY_200);
    }
  }
  while(digitalRead(PIN_BOTON_ROTAR) == LOW){
  }
}

void configurarEntradas(){
  pinMode(OBJETO_IZQUIERDA, INPUT);
  pinMode(OBJETO_IZQUIERDA_MEDIO, INPUT);
  pinMode(OBJETO_MEDIO, INPUT);
  pinMode(OBJETO_DERECHA_MEDIO, INPUT);
  pinMode(OBJETO_DERECHA, INPUT);
  pinMode(PIN_BOTON_ROTAR, INPUT_PULLUP);
  pinMode(PIN_BOTON_SELECCIONAR, INPUT_PULLUP);
}

void configurarMotor(){
  pinMode(ENABLE, OUTPUT);
  digitalWrite (ENABLE, HIGH);
  ledcAttachChannel(PIN_MOTOR_A1, FREC, RES, CHANNEL1); //l_pwm-A
  ledcAttachChannel(PIN_MOTOR_A2, FREC, RES, CHANNEL2); //r_pwm-A
  ledcAttachChannel(PIN_MOTOR_B1, FREC, RES, CHANNEL3); //l_pwm-B
  ledcAttachChannel(PIN_MOTOR_B2, FREC, RES, CHANNEL4); //r_pwm-B
}
void setup(){
  Serial.begin(115200);
  //BT.begin("esp32");
  configurarEntradas();
  configurarMotor();
  //modos_quita = REPOSO;
}
void loop()
{
  sumo();
}
